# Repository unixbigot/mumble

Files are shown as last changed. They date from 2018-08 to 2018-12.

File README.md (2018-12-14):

# Mumble - a very small GRBL

Mumble is a board for [the ESP32 port of GRBL](https://github.com/bdring/Grbl_Esp32), targetted at low-voltage stepper motors. 
It was designed for the Minigraph CNC sticker plotter, but is intended to be usable for other CNC experiments.

It exposes all the GRBL pins, and has three DRV8834 low-votage motor drivers on-board.   
Unlike the more popular A4988, the DRV8834 operates from motor voltage in the range 3v to 10.8v, making it suitable
for low-voltage miniature steppers.

The board also features a lithium battery charge controller.

Change Log,

Issues

Version 1.0 -> 1.3
* Bradley King, fixed double pin 10
* Bradley King, connected enable to vmotor via 47k resistor (datasheet 8.4.3)
* Bradley King, connected charge status led to + v_usb, was floating.

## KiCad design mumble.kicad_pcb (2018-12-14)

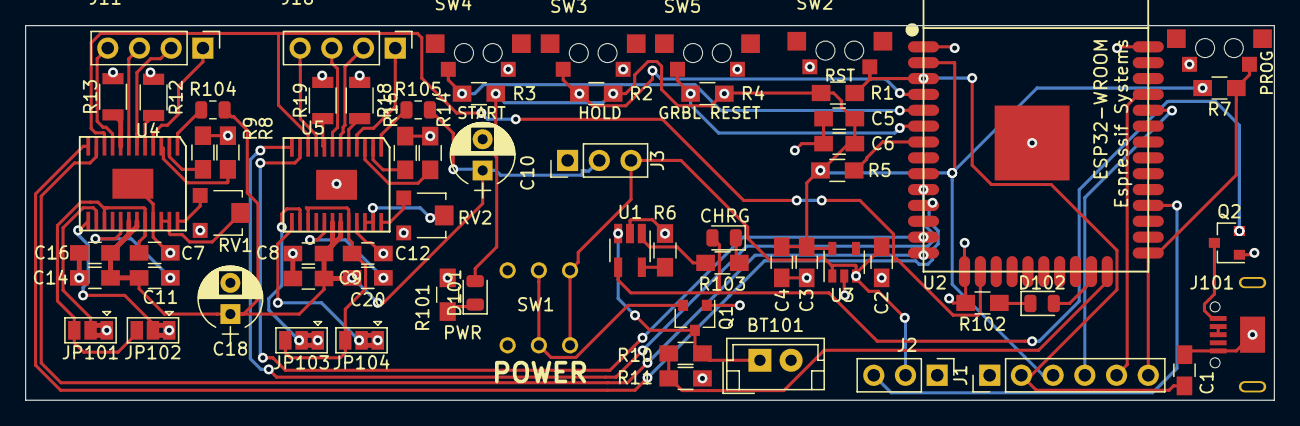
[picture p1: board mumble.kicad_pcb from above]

Board: 2 copper layers, 100.0 x 30.0 mm, 67 parts (0 on the bottom side), 60 nets.

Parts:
BT101: Battery; JST_EH_B02B-EH-A_02x2.50mm_Straight
C1, C5: 0.1uF; C_0805_HandSoldering
C2, C3: 1uF; C_0805_HandSoldering
C4, C6, C8, C14: 10uF; C_0805_HandSoldering
C7, C12: 4.7uF; C_0805_HandSoldering
C9, C16: 2.2uF; C_0805_HandSoldering
C10, C18: 100uF; CP_Radial_D5.0mm_P2.50mm
C11, C20: 0.01uF; C_0805_HandSoldering
D101, D102: LED; LED_0805_2012Metric
D103: CHRG; LED_0805_2012Metric
J1: Serial; PinHeader_1x06_P2.54mm_Vertical
J2: Servo; Pin_Header_Straight_1x03_Pitch2.54mm
J3: VM sel; Pin_Header_Straight_1x03_Pitch2.54mm
J11: X_MOT; Pin_Header_Straight_1x04_Pitch2.54mm
J16: Z_MOT; Pin_Header_Straight_1x04_Pitch2.54mm
J101: USB_B_Micro; USB_Micro
JP101, JP102, JP103, JP104: Jumper_3_Bridged12; SolderJumper-3_P1.3mm_Bridged2Bar12_Pad1.0x1.5mm
Q1, Q2: IRLML9301; SOT-23
R1, R2, R3, R4, R5, R7, R11: 10k; R_0805_HandSoldering
R6: 1.2K; R_0805_HandSoldering
R8, R9, R14, R16: 47k; R_0805_HandSoldering
R10: 50k; R_0805_HandSoldering
R12, R13, R18, R19: 0.1R; R_1206
R101, R102, R103: 330; R_0805_HandSoldering
R104, R105: 47k; R_0805_2012Metric
RV1, RV2: 10k; Potentiometer_Trimmer-EVM3E
SW1: SW_SPST; CherryPowerSwitch
SW2: Reset; TVBM02
SW3: Hold Button; TVBM02
SW4: Start Button; TVBM02
SW5: Abort Button; TVBM02
SW6: Program; TVBM02
U1: TP4054; SOT-23-5_HandSoldering
U2: ESP32-WROOM
U3: AP2204K-3.3; SOT-23-5
U4, U5: DRV8834; HTSSOP-24

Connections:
+3V3: C3.1, C4.1, C5.1, C6.1, D101.2, J1.3, R1.2, R2.1, R3.1, R4.1, R5.1, R7.2, U2.2, U3.5
+BATT: BT101.1, Q1.3, R10.1, U1.3
/BATT_PROT: D103.2, Q2.2, U1.4
/BATT_SWITCHED: C2.1, J2.2, J3.3, SW1.1, U3.1, U3.3
/BATT_VOLT: R10.2, R11.1, U2.24
/CHRG_ST: R103.2, U1.1
/DOOR: R5.2, U2.7
/GPIO15: D102.2, U2.23
/GRBL_RESET: R4.2, SW5.1, U2.6
/HOLD: R2.2, SW3.1, U2.4
/PROGRAM: J1.6, R7.1, SW6.2, U2.25
/RESET: C1.1, J1.2, R1.1, SW2.2, U2.3
/SERVO: J2.3, U2.28
/START: R3.2, SW4.1, U2.5
/STEP_EN: U2.16, U4.10, U5.10
/UART_RX: J1.4, U2.34
/UART_TX: J1.5, U2.35
/VCP_X: C11.1, U4.17
/VCP_Y: C20.1, U5.17
/VINT_X: C7.1, JP101.3, JP102.3, U4.15, U4.20
/VINT_Y: C12.1, JP103.3, JP104.3, U5.15, U5.20
/VM: C8.1, C9.1, C10.1, C11.2, C14.1, C16.1, C18.1, C20.2, J3.2, R104.2, R105.2, U4.18, U4.19, U5.18, U5.19
/X_DIR: U2.11, U4.12
/X_STEP: U2.14, U4.11
/Y_DIR: U2.10, U5.12
/Y_STEP: U2.13, U5.11
GND: BT101.2, C1.2, C2.2, C3.2, C4.2, C5.2, C6.2, C7.2, C8.2, C9.2, C10.2, C12.2, C14.2, C16.2, C18.2, J1.1, J2.1, J3.1, J101.5, J101.6, JP101.1, JP102.1, JP103.1, JP104.1, Q1.1, Q2.1, R6.2, R8.2, R9.2, R11.2, R12.1, R13.1, R14.2, R16.2, R18.1, R19.1, R101.2, R102.2, RV1.3, RV2.3, SW2.1, SW3.2, SW4.2, SW5.2, SW6.1, U1.2, U2.1, U2.15, U2.38, U2.39, U3.2, U4.21, U4.25, U5.21, U5.25
unnamed: D101.1, R101.1
unnamed: D102.1, R102.1
unnamed: D103.1, R103.1
unnamed: J11.1, U4.4
unnamed: J11.2, U4.6
unnamed: J11.3, U4.7
unnamed: J11.4, U4.9
unnamed: J16.1, U5.4
unnamed: J16.2, U5.6
unnamed: J16.3, U5.7
unnamed: J16.4, U5.9
unnamed: J101.1, Q2.3
unnamed: J101.2, J101.3
unnamed: JP101.2, U4.14
unnamed: JP102.2, U4.13
unnamed: JP103.2, U5.14
unnamed: JP104.2, U5.13
unnamed: Q1.2, SW1.2
unnamed: R6.1, U1.5
unnamed: R8.1, U4.3
unnamed: R9.1, U4.2
unnamed: R12.2, U4.5
unnamed: R13.2, U4.8
unnamed: R14.1, U5.3
unnamed: R16.1, U5.2
unnamed: R18.2, U5.5
unnamed: R19.2, U5.8
unnamed: R104.1, U4.1
unnamed: R105.1, U5.1
unnamed: RV1.1, U4.24
unnamed: RV1.2, U4.22, U4.23
unnamed: RV2.1, U5.24
unnamed: RV2.2, U5.22, U5.23

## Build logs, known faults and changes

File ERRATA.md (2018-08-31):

# Mumble Errata

## V1.0
### Fixed
* ~J1 RTS and DTR are swapped, should use RTS=reset DTR=prog (design error)~
* ~No "hello world" LED (design improvement)~
* ~Servo power should connect to vBAT? (design error)~
* ~Order of buttons: [start, hold, abort (grbl reset), reset, (esp) program] (layout improvement)~
* ~Footprint for motor drivers has pins too close~

### To fix
* USB footprint does not have mid-placed pads for alternate connector (layout improvement)

### Notes
* Large switch pads are not connected (layout improvement)
*	- On switches ordered large pads are shorted (chassis).

## V1.1
### To fix
* X motor driver has 3 pins shorted (X_STEP, X_DIR, Pin 12)
* VINT Label goes nowhere and should go to internal driver regulator VINT pin

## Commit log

2018-08-02 Minigraph - a CNC sticker plotter
    [mumble.sch]
2018-08-03 Routed PCB
    [mumble.kicad_pcb, mumble.sch]
2018-08-03 Updated caps and sense resistors
    [mumble.kicad_pcb, mumble.sch]
2018-08-17 Updated some of the errata
    [_saved_mumble.sch, mumble.kicad_pcb]
2018-08-19 Updated power button and USB connector
    [mumble.kicad_pcb, mumble.sch]
2018-08-19 Actually saved the PCB this time
    [_saved_mumble.sch, mumble.kicad_pcb]
2018-08-31 Updated to V1.2 of PCB
    [_saved_mumble.sch, mumble.kicad_pcb, mumble.sch]
2018-11-13 added interactive BOM
2018-12-14 version 1.3, fixed nsleep, chrg led not working. change motor pinout for neater routing.
    [mumble.kicad_pcb, mumble.sch]
